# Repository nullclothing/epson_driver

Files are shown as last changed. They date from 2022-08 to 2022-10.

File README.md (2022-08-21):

# Epson Printhead Driver

This is a driver for Epson piezo inkjet printheads, based heavily on Joyce G. Kwan's prior work. It provides a PMOD interface for use with FPGA development boards such as the [iCEBreaker](https://1bitsquared.com/collections/fpga/products/icebreaker). The goal is to enable use of cheap and widespread Epson printheads in DIY projects.

These printheads require an analog signal to actuate the piezos. This signal is actually fairly high voltage/power. It peaks around 33V, and if you're activating all nozzles, you can be supplying over 3A to the printhead. Therefore, we need a DAC with an amplifier capable of supplying that much power. This makes up the bulk of the project.

## Tested on

* Epson XP4105

## References

* [Joyce Kwan's Master's Thesis](https://dspace.mit.edu/bitstream/handle/1721.1/85435/870681346-MIT.pdf?sequence=2_1)

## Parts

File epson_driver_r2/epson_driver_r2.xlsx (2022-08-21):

Prj: | printhead_controller.xml |  |  |  | Board Qty: | 1
Co.: |  |  |  |  | Unit Cost: | $60.84
Prj date: | 7/31/2022 6:24:15 PM |  |  |  | Total Cost: | $60.84 |  |  |  |  | $39.21 | 14 of 32 parts found |  |  |  |  | $61.50 | 28 of 32 parts found
$ date: | 2022-07-31 18:26:09
Global Part Info |  |  |  |  |  |  | Digi-Key |  |  |  |  |  | Mouser
Refs | Value | Footprint | Manf# | Qty | Unit$ | Ext$ | Avail | Purch | Unit$ | MOQ | Ext$ | Cat# | Avail | Purch | Unit$ | MOQ | Ext$ | Cat#
C1,C2 | 22uF | CP_Elec_6.3x7.7 | EEE-FN1J220XP | 2 | $0.770 | $1.54 |  |  |  |  |  |  | 9238 |  | $0.770 | 1 | $1.54 | 667-EEE-FN1J220XP (https://www.mouser.com/ProductDetail/Panasonic/EEE-FN1J220XP?qs=OlC7AqGiEDlUzF6cEuRRyQ%3D%3D)
C3,C4 | 100nF | C_0603_1608Metric_Pad1.08x0.95mm_HandSolder | CS0603KRX7R9BB104 | 2 | $0.160 | $0.32 |  |  |  |  |  |  | 23727 |  | $0.160 | 1 | $0.32 | 603-CS0603KRX79BB104 (https://www.mouser.com/ProductDetail/YAGEO/CS0603KRX7R9BB104?qs=tS%2FAHvPQ%2F54ugNwFbI0Low%3D%3D)
C5,C6,C10,C13,C14,C16,C20,C21 | 4.7uF | C_1206_3216Metric_Pad1.33x1.80mm_HandSolder | GRM31CC72A475ME11L | 8 | $0.850 | $6.80 | 35548 |  | $0.850 | 1 | $6.80 | 490-18621-1-ND (https://octopart.com/click/track?ai=8078&sig=059bb32&sid=459&ppid=102281467&vpid=549482197&ct=offers) | 59445 |  | $0.910 | 1 | $7.28 | 81-GRM31CC72A475ME11 (https://www.mouser.com/ProductDetail/Murata-Electronics/GRM31CC72A475ME11L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)
C7,C8 | 10nF | C_0603_1608Metric_Pad1.08x0.95mm_HandSolder | GCM188R71H103KA37J | 2 | $0.100 | $0.20 | 1087679 |  | $0.100 | 1 | $0.20 | 490-11159-1-ND (https://octopart.com/click/track?ai=8078&sig=0faa127&sid=459&ppid=19777506&vpid=216077861&ct=offers) | 4921081 |  | $0.100 | 1 | $0.20 | 81-GCM188R71H103KA7J (https://www.mouser.com/ProductDetail/Murata-Electronics/GCM188R71H103KA37J?qs=N3Kl9KD794T3%2FxlXdF0Axg%3D%3D)
C9,C11,C15,C19 | 2.2uF | C_0603_1608Metric_Pad1.08x0.95mm_HandSolder | GRT188R61H225KE13D | 4 | $0.310 | $1.24 | 147813 |  | $0.310 | 1 | $1.24 | 490-12332-1-ND (https://octopart.com/click/track?ai=8078&sig=02d8b98&sid=459&ppid=62921612&vpid=223635534&ct=offers) | 32011 |  | $0.330 | 1 | $1.32 | 81-GRT188R61H225KE3D (https://www.mouser.com/ProductDetail/Murata-Electronics/GRT188R61H225KE13D?qs=drgMNd%252BkGPOTrTm4FN7APg%3D%3D)
C12 | 100n | C_0603_1608Metric_Pad1.08x0.95mm_HandSolder | CS0603KRX7R9BB104 | 1 | $0.160 | $0.16 |  |  |  |  |  |  | 23727 |  | $0.160 | 1 | $0.16 | 603-CS0603KRX79BB104 (https://www.mouser.com/ProductDetail/YAGEO/CS0603KRX7R9BB104?qs=tS%2FAHvPQ%2F54ugNwFbI0Low%3D%3D)
C17,C18 | 20pF | C_0603_1608Metric_Pad1.08x0.95mm_HandSolder | CL10C200JB81PNC | 2 | $0.110 | $0.22 |  |  |  |  |  |  | 63811 |  | $0.110 | 1 | $0.22 | 81-GRM185C1H200JA01J (https://www.mouser.com/ProductDetail/Murata-Electronics/GRM1885C1H200JA01J?qs=SSucg2PyLi5AT43tSDep3g%3D%3D)
D1 | CD1206-B2100 | D_1206_3216Metric_Pad1.42x1.75mm_HandSolder | CD1206-B2100 | 1 | $0.480 | $0.48 | 5916 |  | $0.480 | 1 | $0.48 | CD1206-B2100CT-ND (https://octopart.com/click/track?ai=8078&sig=08d7e77&sid=459&ppid=2021213&vpid=241887145&ct=offers) | 60953 |  | $0.480 | 1 | $0.48 | 652-CD1206-B2100 (https://www.mouser.com/ProductDetail/Bourns/CD1206-B2100?qs=VNGG2InBe5EQUAtP9HPU9g%3D%3D)
F1 | Fuse | Fuse_1206_3216Metric_Pad1.42x1.75mm_HandSolder | SF-1206F400M-2 | 1 | $0.800 | $0.80 | 2972 |  | $0.810 | 1 | $0.81 | 118-SF-1206F400M-2CT-ND (https://octopart.com/click/track?ai=8078&sig=0ee56f3&sid=459&ppid=118747778&vpid=734376597&ct=offers) | 4396 |  | $0.800 | 1 | $0.80 | 652-SF-1206F400M-2 (https://www.mouser.com/ProductDetail/Bourns/SF-1206F400M-2?qs=QNEnbhJQKvZR8N5n9OuamA%3D%3D)
H1,H2 | MountingHole_Pad | MountingHole_3.2mm_M3_Pad_TopBottom |  | 2
J1 | Barrel_Jack | BarrelJack_CUI_PJ-063AH_Horizontal | PJ-063AH | 1 | $1.580 | $1.58 | 9103 |  | $1.590 | 1 | $1.59 | CP-063AH-ND (https://octopart.com/click/track?ai=8078&sig=06ca8e5&sid=459&ppid=106234056&vpid=612419883&ct=offers) | 6973 |  | $1.580 | 1 | $1.58 | 490-PJ-063AH (https://www.mouser.com/ProductDetail/CUI-Devices/PJ-063AH?qs=WyjlAZoYn51bQfA53nMcVA%3D%3D)
J2,J3 | PMOD | PMOD-12-PERIPHERAL | 68021-212HLF (https://www.digilentinc.com/Pmods/Digilent-Pmod_%20Interface_Specification.pdf) | 2 | $1.380 | $2.76 |  |  |  |  |  |  | 2209 |  | $1.380 | 1 | $2.76 | 649-68021-212HLF (https://www.mouser.com/ProductDetail/Amphenol-FCI/68021-212HLF?qs=KWzNV0LRuGB%252BcFlfC6ZyTw%3D%3D)
JP1 | SolderJumper_3_Open | SolderJumper-3_P1.3mm_Open_Pad1.0x1.5mm |  | 1
L1 | LPS5030-223MRC | L_Coilcraft_LPS5030 | LPS5030-223MRC | 1 | $1.440 | $1.44 |  |  |  |  |  |  | 4993 |  | $1.440 | 1 | $1.44 | 994-LPS5030-223MRC (https://www.mouser.com/ProductDetail/Coilcraft/LPS5030-223MRC?qs=QQJxVsr8EGaw%252Bi6Jfb4hJQ%3D%3D)
Q1,Q2 | CMPT2222 | SOT-23 | CMPT2222AE TR PBFREE (https://www.onsemi.com/pub/Collateral/BC808-D.pdf) | 2 | $0.580 | $1.16 |  |  |  |  |  |  | 10799 |  | $0.580 | 1 | $1.16 | 610-CMPT2222AE (https://www.mouser.com/ProductDetail/Central-Semiconductor/CMPT2222AE-TR-PBFREE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)
Q3,Q5 | MJD122 | TO-252-3_TabPin2 | MJD122G | 2 | $0.850 | $1.70 | 1310 |  | $0.850 | 1 | $1.70 | MJD122GOS-ND (https://octopart.com/click/track?ai=8078&sig=0a2e7f9&sid=459&ppid=1003846&vpid=33529186&ct=offers) | 840 |  | $0.890 | 1 | $1.78 | 863-MJD122G (https://www.mouser.com/ProductDetail/onsemi/MJD122G?qs=HVbQlW5zcXU7nyhrpyySSg%3D%3D)
Q4,Q6 | MJD128 | TO-252-3_TabPin2 | MJD128T4G | 2 | $0.970 | $1.94 |  |  |  |  |  |  | 80 |  | $0.970 | 1 | $1.94 | 863-MJD128T4G (https://www.mouser.com/ProductDetail/onsemi/MJD128T4G?qs=R2UZ7gjkEjJ3iLJVIIxt5Q%3D%3D)
R1,R2,R4,R11,R12 | 10k | R_0603_1608Metric_Pad0.98x0.95mm_HandSolder | CMP0603AFX-1002ELF | 5 | $0.280 | $1.40 | 47739 |  | $0.280 | 1 | $1.40 | 118-CMP0603AFX-1002ELFCT-ND (https://octopart.com/click/track?ai=8078&sig=0564ef3&sid=459&ppid=107945381&vpid=626855334&ct=offers) | 18728 |  | $0.280 | 1 | $1.40 | 652-CMP0603AFX-1002L (https://www.mouser.com/ProductDetail/Bourns/CMP0603AFX-1002ELF?qs=TiOZkKH1s2Q14lKL9rbzLg%3D%3D)
R3 | 100k | R_0603_1608Metric_Pad0.98x0.95mm_HandSolder | CHV0603-FX-1003EST | 1 | $0.530 | $0.53 | 5000 |  | $0.540 | 1 | $0.54 | 118-CHV0603-FX-1003ESTCT-ND (https://octopart.com/click/track?ai=8078&sig=0018dc4&sid=459&ppid=119150998&vpid=725062019&ct=offers) | 31365 |  | $0.530 | 1 | $0.53 | 652-CHV0603FX1003EST (https://www.mouser.com/ProductDetail/Bourns/CHV0603-FX-1003EST?qs=QNEnbhJQKvYjZUOCb6w1iw%3D%3D)
R5 | 2.8k | R_0603_1608Metric_Pad0.98x0.95mm_HandSolder | RN73H1JTTD2801B25 | 1 | $0.150 | $0.15 | 5943 |  | $0.150 | 1 | $0.15 | 13-RT0603DRE072R8LCT-ND (https://octopart.com/click/track?ai=8078&sig=0e7af4d&sid=459&ppid=88499069&vpid=634400164&ct=offers) | 7048 |  | $0.160 | 1 | $0.16 | 603-RT0603DRE072R8L (https://www.mouser.com/ProductDetail/YAGEO/RT0603DRE072R8L?qs=UG%2F8xqv%2F6WexsJAtHa5TmQ%3D%3D)
R6 | 124k | R_0603_1608Metric_Pad0.98x0.95mm_HandSolder | CR0603-FX-1243ELF | 1 | $0.100 | $0.10 |  |  |  |  |  |  | 50378 |  | $0.100 | 1 | $0.10 | 652-CR0603FX-1243ELF (https://www.mouser.com/ProductDetail/Bourns/CR0603-FX-1243ELF?qs=e7cxVwPieup%252BZlccaQO2Sw%3D%3D)
R7,R8 | 1k | R_0603_1608Metric_Pad0.98x0.95mm_HandSolder | RK73H1JTTD1001F | 2 | $0.100 | $0.20 | 9057089 |  | $0.100 | 1 | $0.20 | 2019-RK73H1JTTD1001FCT-ND (https://octopart.com/click/track?ai=8078&sig=0cfd3be&sid=459&ppid=2166374&vpid=531266076&ct=offers) | 2939001 |  | $0.100 | 1 | $0.20 | 660-RK73H1JTTD1001F (https://www.mouser.com/ProductDetail/KOA-Speer/RK73H1JTTD1001F?qs=LDe0C6QMEhjxBAtFZK22kg%3D%3D)
R9,R10 | 13.2k | R_0603_1608Metric_Pad0.98x0.95mm_HandSolder | RN731JTTD1322D25 | 2 | $0.310 | $0.62 |  |  |  |  |  |  | 4178 |  | $0.310 | 1 | $0.62 | 660-RN731JTTD1322D25 (https://www.mouser.com/ProductDetail/KOA-Speer/RN731JTTD1322D25?qs=FP1Nkeq3mZ%252BTq1KDbgJMDg%3D%3D)
RV1,RV2 | 10k | Potentiometer_Bourns_3214G_Horizontal | 3214G-1-103E | 2 | $2.760 | $5.52 | 460 |  | $3.070 | 1 | $6.14 | 3214G-1-103ECT-ND (https://octopart.com/click/track?ai=8078&sig=031dd45&sid=459&ppid=974184&vpid=34262155&ct=offers) | 1098 |  | $2.760 | 1 | $5.52 | 652-3214G-1-103E (https://www.mouser.com/ProductDetail/Bourns/3214G-1-103E?qs=2EY8XwU7iu%2FCUewmLosCUg%3D%3D)
TP1,TP2 | TestPoint | TestPoint_Pad_D1.0mm |  | 2
U1 | AD5428 | TSSOP-20_4.4x6.5mm_P0.65mm | AD5428YRUZ (https://www.analog.com/media/en/technical-documentation/data-sheets/AD5428_5440_5447.pdf) | 1 | $7.190 | $7.19 | 28 |  | $7.190 | 1 | $7.19 | 505-AD5428YRUZ-ND (https://octopart.com/click/track?ai=8078&sig=02304d4&sid=459&ppid=434837&vpid=771422796&ct=offers) | 115 |  | $7.190 | 1 | $7.19 | 584-AD5428YRUZ (https://www.mouser.com/ProductDetail/Analog-Devices/AD5428YRUZ?qs=NmRFExCfTkE3wTpc%2Fxg%252Btw%3D%3D)
U2 | XP4105_Printhead | Molex_200528-0210_1x21-1MP_P1.00mm_Horizontal | 200528-0210 (http://datasheet.octopart.com/2005280210-Molex-datasheet-147949751.pdf) | 1 |  |  |  |  |  |  |  |  | NonStk |  |  |  |  | N/A (https://www.mouser.com/ProductDetail/Molex/2005280210?qs=doiCPypUmgGMhsUUsBtF7g%3D%3D)
U3 | LT3060 | SOT-23-8_Handsoldering | LT3060ETS8-2.5#TRMPBF (https://www.mouser.com/datasheet/2/609/lt3060-2821776.pdf) | 1 | $3.710 | $3.71 |  |  |  |  |  |  | 498 |  | $3.710 | 1 | $3.71 | 584-3060ETS8-2.5TMPF (https://www.mouser.com/ProductDetail/Analog-Devices/LT3060ETS8-2.5TRMPBF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)
U4 | ADP7142AUJZ-3.3 | TSOT-23-5 | ADP7142AUJZ-3.3-R7 (https://www.analog.com/media/en/technical-documentation/data-sheets/ADP7142.pdf) | 1 | $3.710 | $3.71 |  |  |  |  |  |  | 3522 |  | $3.710 | 1 | $3.71 | 584-ADP7142AUJZ3.3R7 (https://www.mouser.com/ProductDetail/Analog-Devices/ADP7142AUJZ-3.3-R7?qs=hpwIUhX6lWzL3aTPGC3rIQ%3D%3D)
U5 | MP2459 | TSOT-23-6_HandSoldering | MP2459GJ-Z (https://www.mouser.com/datasheet/2/277/MP2459GJ_Z-2945766.pdf) | 1 | $1.430 | $1.43 |  |  |  |  |  |  | 23764 |  | $1.430 | 1 | $1.43 | 946-MP2459GJZ (https://www.mouser.com/ProductDetail/Monolithic-Power-Systems-MPS/MP2459GJ-Z?qs=QEkzKklKf2TCowgo8xAXMA%3D%3D)
U6 | LM4132xMF-2.5 | SOT-23-5 | LM4132CMFX-2.5/NOPB (http://www.ti.com/lit/ds/symlink/lm4132.pdf) | 1 | $3.170 | $3.17 |  |  |  |  |  |  | 2610 |  | $3.170 | 1 | $3.17 | 926-LM4132CMFX25NOPB (https://www.mouser.com/ProductDetail/Texas-Instruments/LM4132CMFX-2.5-NOPB?qs=QbsRYf82W3H50M9m7eepXQ%3D%3D)
U7 | LT1632 | SOIC-8_3.9x4.9mm_P1.27mm | LT1632IS8#TRPBF (http://datasheet.octopart.com/LT1632IS8%23TRPBF-Analog-Devices-datasheet-12698536.pdf) | 1 | $10.770 | $10.77 | 13985 |  | $10.770 | 1 | $10.77 | LT1632IS8#TRPBFCT-ND (https://octopart.com/click/track?ai=8078&sig=0346e9e&sid=459&ppid=88938581&vpid=650437325&ct=offers) | 2480 |  | $10.780 | 1 | $10.78 | 584-LT1632IS8#TRPBF (https://www.mouser.com/ProductDetail/Analog-Devices/LT1632IS8TRPBF?qs=ytflclh7QUWs56oPf2mA9w%3D%3D)
 |  |  |  |  | Total Purchase: | $0.00 | Buy here (https://www.digikey.com/ordering/shoppingcart) |  |  |  | $0.00 |  | Buy here (https://mouser.com/bom/) |  |  |  | $0.00
KiCost® v1.1.11 |  |  |  |  | Purchase description:

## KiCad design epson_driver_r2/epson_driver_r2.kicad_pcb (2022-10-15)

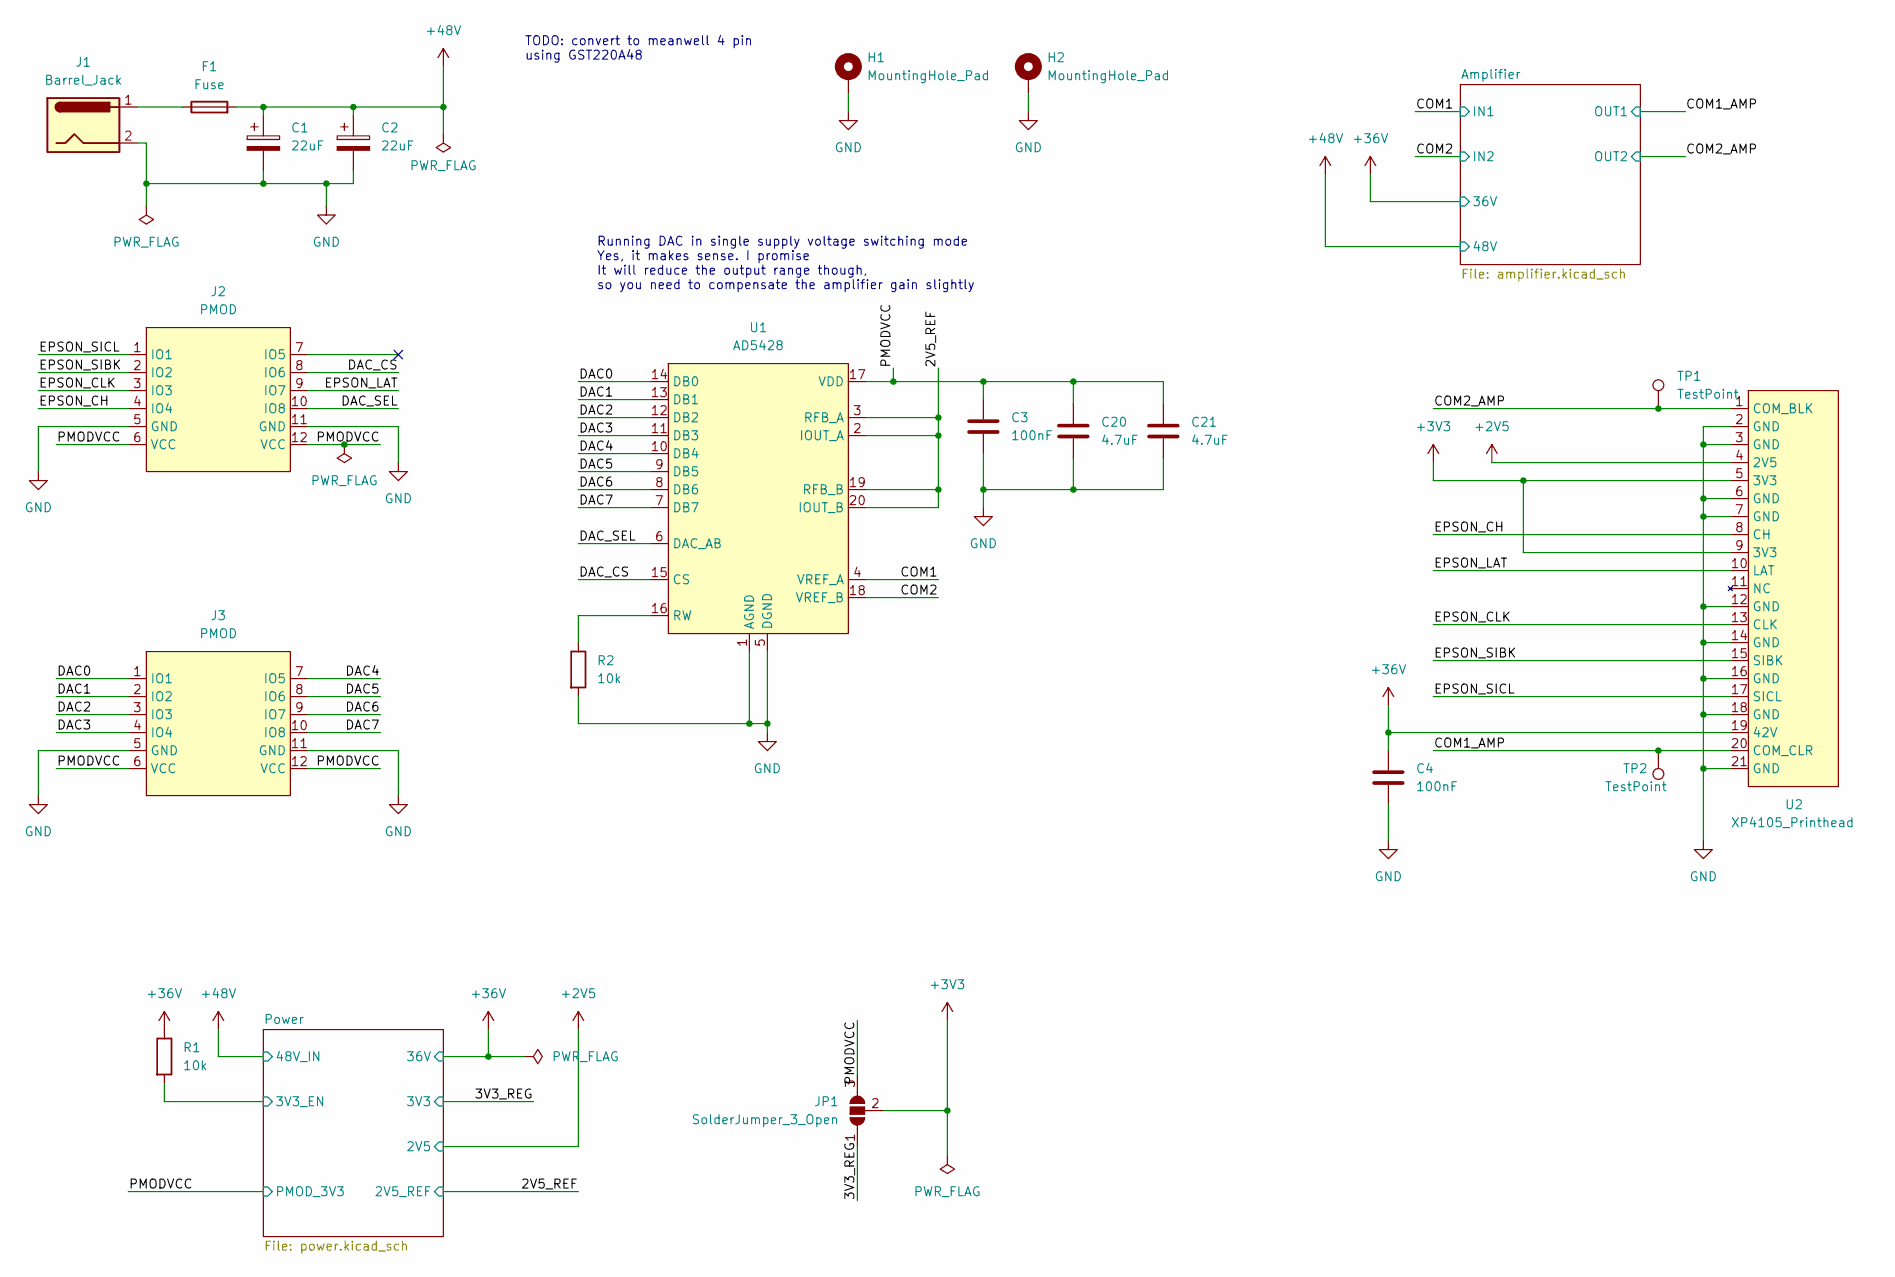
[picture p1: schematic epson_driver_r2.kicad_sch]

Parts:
C1, C2: 22uF; CP_Elec_6.3x7.7
C3, C4: 100nF; C_0603_1608Metric_Pad1.08x0.95mm_HandSolder
C20, C21: 4.7uF; C_1206_3216Metric_Pad1.33x1.80mm_HandSolder
F1: Fuse; Fuse_1206_3216Metric_Pad1.42x1.75mm_HandSolder
H1, H2: MountingHole_Pad; MountingHole_3.2mm_M3_Pad_TopBottom
J1: Barrel_Jack; BarrelJack_CUI_PJ-063AH_Horizontal
J2, J3: PMOD; PMOD-12-PERIPHERAL
JP1: SolderJumper_3_Open; SolderJumper-3_P1.3mm_Open_Pad1.0x1.5mm
R1, R2: 10k; R_0603_1608Metric_Pad0.98x0.95mm_HandSolder
TP1, TP2: TestPoint; TestPoint_Pad_D1.0mm
U1: AD5428; TSSOP-20_4.4x6.5mm_P0.65mm
U2: XP4105_Printhead; Molex_200528-0210_1x21-1MP_P1.00mm_Horizontal

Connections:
+2V5: U2.4 (2V5); also elsewhere on the board
+3V3: JP1.2 (C), U2.5 (3V3), U2.9 (3V3)
+36V: C4.1, R1.1, U2.19 (42V); also elsewhere on the board
+48V: C1.1, C2.1, F1.2; also elsewhere on the board
/2V5_REF: U1.2 (IOUT_A), U1.3 (RFB_A), U1.19 (RFB_B), U1.20 (IOUT_B); also elsewhere on the board
/3V3_REG: JP1.1 (A); also elsewhere on the board
/COM1: U1.4 (VREF_A); also elsewhere on the board
/COM1_AMP: TP2.1, U2.20 (COM_CLR); also elsewhere on the board
/COM2: U1.18 (VREF_B); also elsewhere on the board
/COM2_AMP: TP1.1, U2.1 (COM_BLK); also elsewhere on the board
/DAC0: J3.1 (IO1), U1.14 (DB0)
/DAC1: J3.2 (IO2), U1.13 (DB1)
/DAC2: J3.3 (IO3), U1.12 (DB2)
/DAC3: J3.4 (IO4), U1.11 (DB3)
/DAC4: J3.7 (IO5), U1.10 (DB4)
/DAC5: J3.8 (IO6), U1.9 (DB5)
/DAC6: J3.9 (IO7), U1.8 (DB6)
/DAC7: J3.10 (IO8), U1.7 (DB7)
/DAC_CS: J2.8 (IO6), U1.15 (CS)
/DAC_SEL: J2.10 (IO8), U1.6 (DAC_AB)
/EPSON_CH: J2.4 (IO4), U2.8 (CH)
/EPSON_CLK: J2.3 (IO3), U2.13 (CLK)
/EPSON_LAT: J2.9 (IO7), U2.10 (LAT)
/EPSON_SIBK: J2.2 (IO2), U2.15 (SIBK)
/EPSON_SICL: J2.1 (IO1), U2.17 (SICL)
/PMODVCC: C3.1, C20.1, C21.1, J2.6 (VCC), J2.12 (VCC), J3.6 (VCC), J3.12 (VCC), JP1.3 (B), U1.17 (VDD); also elsewhere on the board
/Power/3V3_EN: R1.2; also elsewhere on the board
GND: C1.2, C2.2, C3.2, C4.2, C20.2, C21.2, H1.1, H2.1, J1.2, J2.5 (GND), J2.11 (GND), J3.5 (GND), J3.11 (GND), R2.2, U1.1 (AGND), U1.5 (DGND), U2.2 (GND), U2.3 (GND), U2.6 (GND), U2.7 (GND), U2.12 (GND), U2.14 (GND), U2.16 (GND), U2.18 (GND), U2.21 (GND); also elsewhere on the board
unnamed: F1.1, J1.1
unnamed: R2.1, U1.16 (RW)

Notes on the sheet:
Running DAC in single supply voltage switching mode Yes, it makes sense. I promise It will reduce the output range though, so you need to compensate the amplifier gain slightly
TODO: convert to meanwell 4 pin using GST220A48

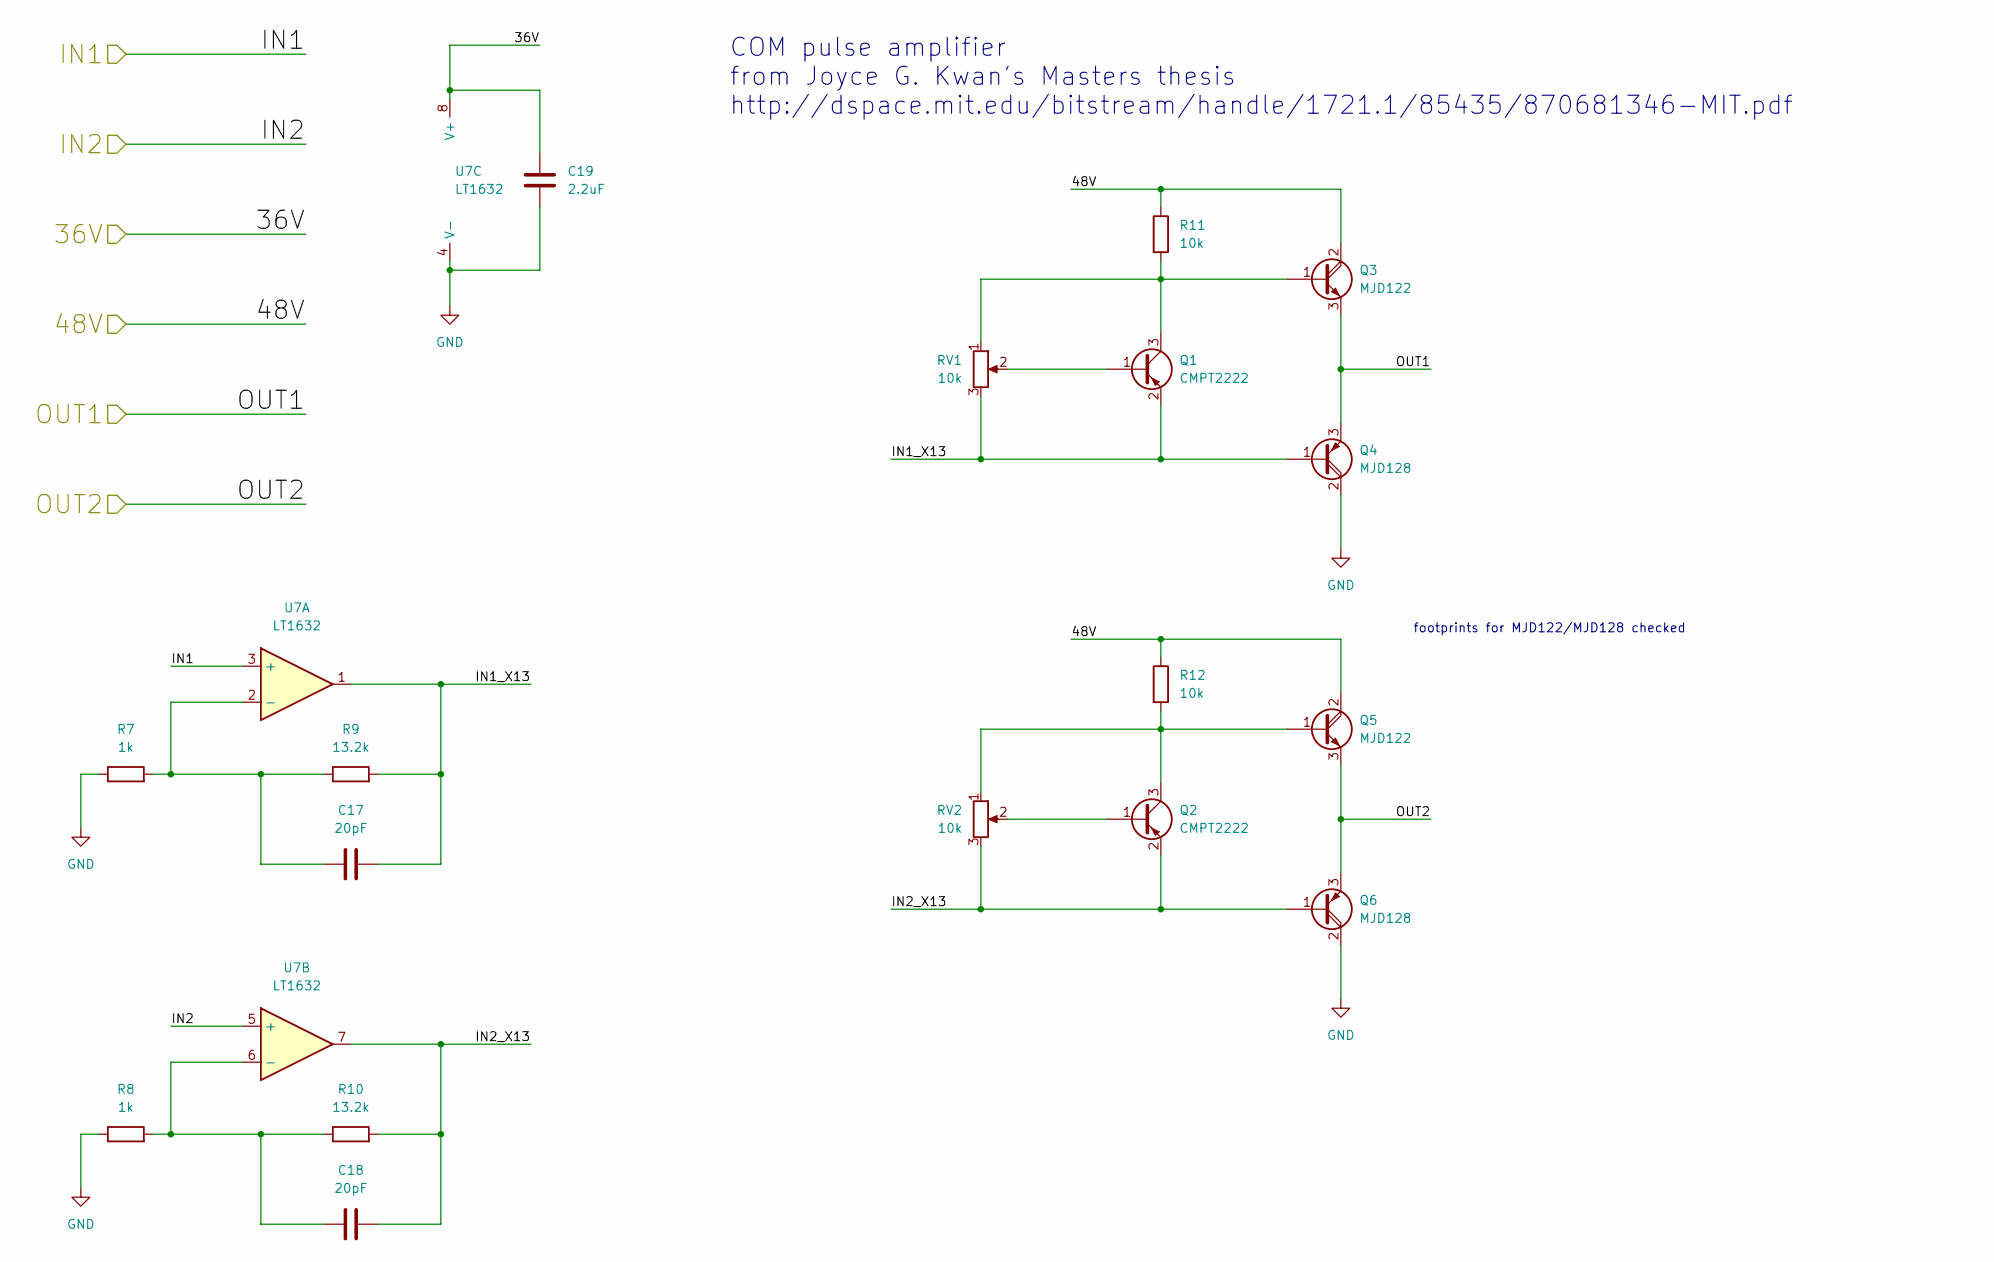
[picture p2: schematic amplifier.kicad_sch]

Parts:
C17, C18: 20pF; C_0603_1608Metric_Pad1.08x0.95mm_HandSolder
C19: 2.2uF; C_0603_1608Metric_Pad1.08x0.95mm_HandSolder
Q1, Q2: CMPT2222; SOT-23
Q3, Q5: MJD122; TO-252-3_TabPin2
Q4, Q6: MJD128; TO-252-3_TabPin2
R7, R8: 1k; R_0603_1608Metric_Pad0.98x0.95mm_HandSolder
R9, R10: 13.2k; R_0603_1608Metric_Pad0.98x0.95mm_HandSolder
R11, R12: 10k; R_0603_1608Metric_Pad0.98x0.95mm_HandSolder
RV1, RV2: 10k; Potentiometer_Bourns_3214G_Horizontal
U7: LT1632; SOIC-8_3.9x4.9mm_P1.27mm

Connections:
+36V: C19.1, U7.8 (V+); also elsewhere on the board
+48V: Q3.2 (C), Q5.2 (C), R11.1, R12.1; also elsewhere on the board
/Amplifier/IN1_X13: C17.2, Q1.2 (E), Q4.1 (B), R9.2, RV1.3, U7.1
/Amplifier/IN2_X13: C18.2, Q2.2 (E), Q6.1 (B), R10.2, RV2.3, U7.7
/COM1: U7.3 (+); also elsewhere on the board
/COM1_AMP: Q3.3 (E), Q4.3 (E); also elsewhere on the board
/COM2: U7.5 (+); also elsewhere on the board
/COM2_AMP: Q5.3 (E), Q6.3 (E); also elsewhere on the board
GND: C19.2, Q4.2 (C), Q6.2 (C), R7.1, R8.1, U7.4 (V-); also elsewhere on the board
unnamed: C17.1, R7.2, R9.1, U7.2 (-)
unnamed: C18.1, R8.2, R10.1, U7.6 (-)
unnamed: Q1.1 (B), RV1.2
unnamed: Q1.3 (C), Q3.1 (B), R11.2, RV1.1
unnamed: Q2.1 (B), RV2.2
unnamed: Q2.3 (C), Q5.1 (B), R12.2, RV2.1

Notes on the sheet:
COM pulse amplifier from Joyce G. Kwan's Masters thesis http://dspace.mit.edu/bitstream/handle/1721.1/85435/870681346-MIT.pdf
footprints for MJD122/MJD128 checked

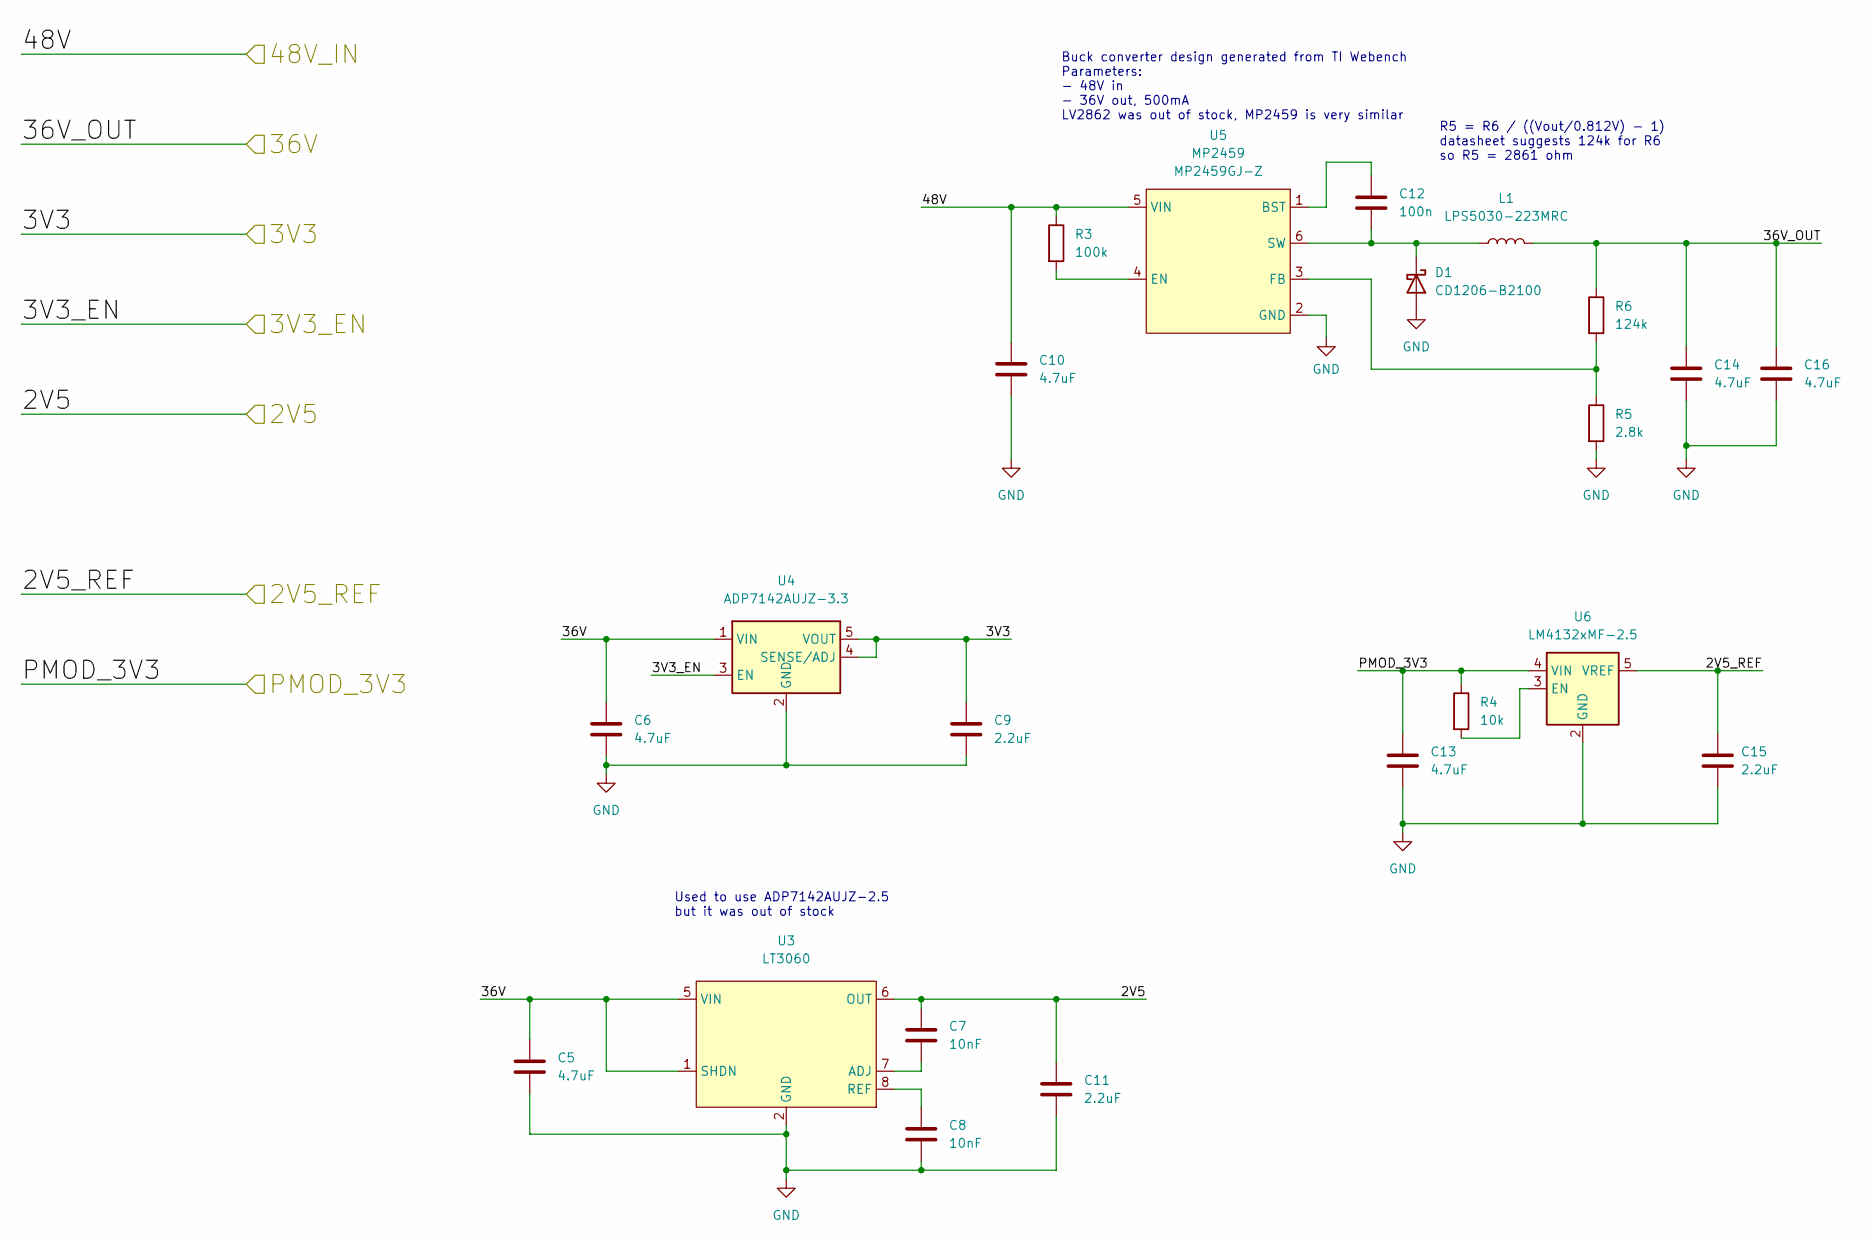
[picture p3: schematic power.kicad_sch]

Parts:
C5, C6, C10, C13, C14, C16: 4.7uF; C_1206_3216Metric_Pad1.33x1.80mm_HandSolder
C7, C8: 10nF; C_0603_1608Metric_Pad1.08x0.95mm_HandSolder
C9, C11, C15: 2.2uF; C_0603_1608Metric_Pad1.08x0.95mm_HandSolder
C12: 100n; C_0603_1608Metric_Pad1.08x0.95mm_HandSolder
D1: CD1206-B2100; D_1206_3216Metric_Pad1.42x1.75mm_HandSolder
L1: LPS5030-223MRC; L_Coilcraft_LPS5030
R3: 100k; R_0603_1608Metric_Pad0.98x0.95mm_HandSolder
R4: 10k; R_0603_1608Metric_Pad0.98x0.95mm_HandSolder
R5: 2.8k; R_0603_1608Metric_Pad0.98x0.95mm_HandSolder
R6: 124k; R_0603_1608Metric_Pad0.98x0.95mm_HandSolder
U3: LT3060; SOT-23-8_Handsoldering
U4: ADP7142AUJZ-3.3; TSOT-23-5
U5: MP2459; TSOT-23-6_HandSoldering
U6: LM4132xMF-2.5; SOT-23-5

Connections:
+2V5: C7.1, C11.1, U3.6 (OUT); also elsewhere on the board
+36V: C5.1, C6.1, C14.1, C16.1, L1.2, R6.1, U3.1 (SHDN), U3.5 (VIN), U4.1 (VIN); also elsewhere on the board
+48V: C10.1, R3.1, U5.5 (VIN); also elsewhere on the board
/2V5_REF: C15.1, U6.5 (VREF); also elsewhere on the board
/3V3_REG: C9.1, U4.4 (SENSE/ADJ), U4.5 (VOUT); also elsewhere on the board
/PMODVCC: C13.1, R4.1, U6.4 (VIN); also elsewhere on the board
/Power/3V3_EN: U4.3 (EN); also elsewhere on the board
GND: C5.2, C6.2, C8.2, C9.2, C10.2, C11.2, C13.2, C14.2, C15.2, C16.2, D1.2 (A), R5.2, U3.2 (GND), U3.3 (GND), U3.4 (GND), U4.2 (GND), U5.2 (GND), U6.2 (GND); also elsewhere on the board
unnamed: C7.2, U3.7 (ADJ)
unnamed: C8.1, U3.8 (REF)
unnamed: C12.1, U5.1 (BST)
unnamed: C12.2, D1.1 (K), L1.1, U5.6 (SW)
unnamed: R3.2, U5.4 (EN)
unnamed: R4.2, U6.3 (EN)
unnamed: R5.1, R6.2, U5.3 (FB)

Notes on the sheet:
Buck converter design generated from TI Webench Parameters: - 48V in - 36V out, 500mA LV2862 was out of stock, MP2459 is very similar
R5 = R6 / ((Vout/0.812V) - 1) datasheet suggests 124k for R6 so R5 = 2861 ohm
Used to use ADP7142AUJZ-2.5 but it was out of stock

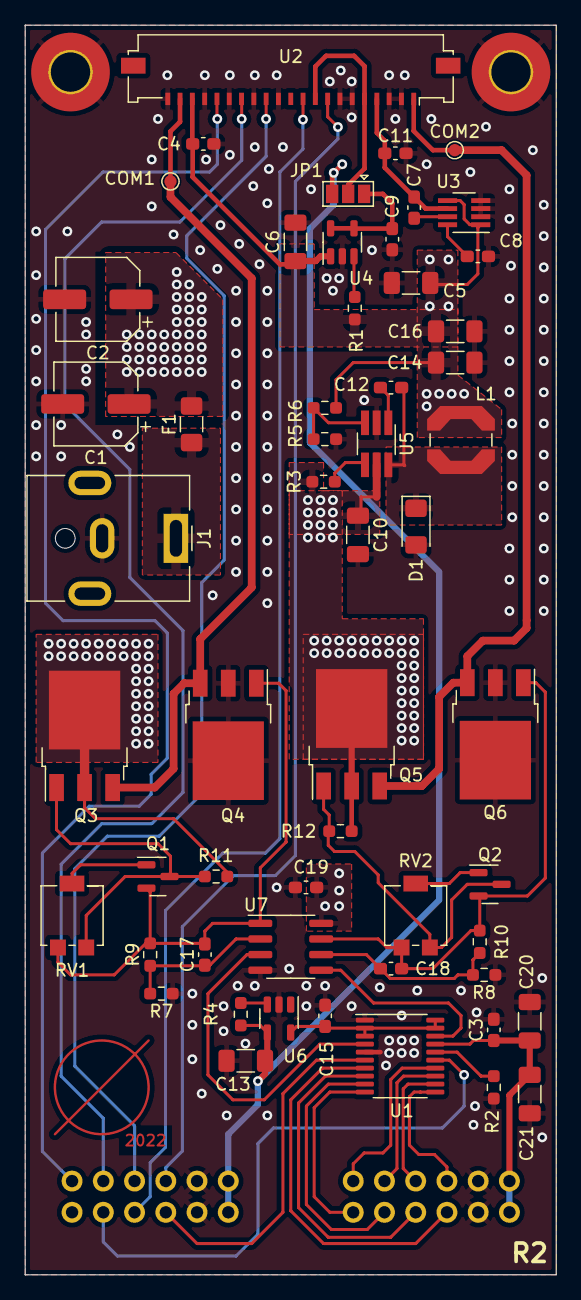
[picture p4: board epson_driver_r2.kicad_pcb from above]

Board: 4 copper layers, 43.2 x 101.6 mm, 59 parts (0 on the bottom side), 45 nets.

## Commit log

2022-08-21 split out epson driver into its own repo
    [amplifier.kicad_sch, epson_driver_r2.kicad_pcb, epson_driver_r2.kicad_sch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]
2022-10-15 make sure flipped PNPs are fixed. need to finalize new board rev
    [amplifier.kicad_sch, epson_driver_r2.kicad_pcb, epson_driver_r2.kicad_sch]
